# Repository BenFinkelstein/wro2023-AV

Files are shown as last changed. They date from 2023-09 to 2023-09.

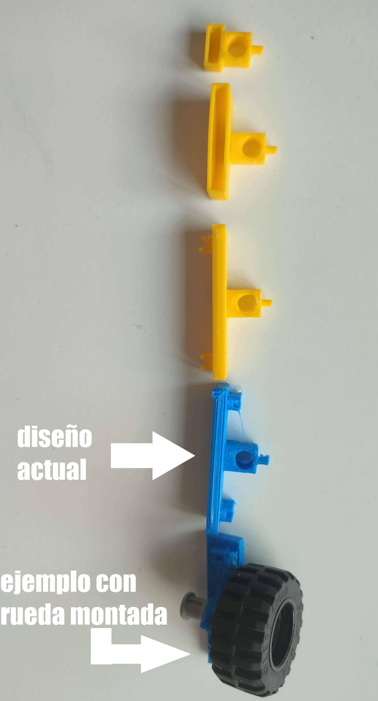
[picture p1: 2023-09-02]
Mobility Management/M.Photos/Montaje de rueda delantera.jpg

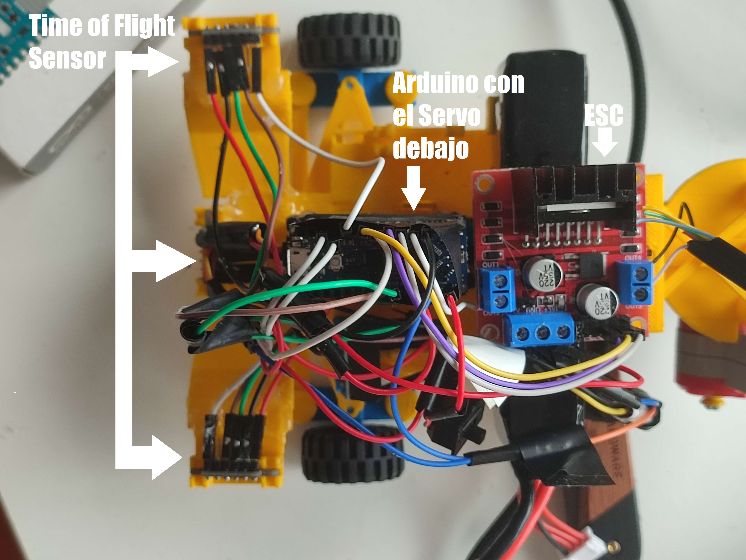
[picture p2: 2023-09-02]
Power and Sense Management/E.Photos/Vista superior de la placa de montaje para los sensores.jpg

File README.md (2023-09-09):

The autonomous vehicle was fully designed from the ground up by the team RoboBros formed by Benjamin Finkelstein Fell and Dimitri Domzalski. 95% of the structures (chassis, steering linkage, sensors board, joints, motor platform, etc.) were printed on a 3D printer. The vehicle is controlled by an Arduino Nano Every. The robot also uses three VL53L0X TOF Sensors, one QMC5883L Magnetometer, one TCS230/TCS3200 Color Sensor, one 13Kg Digital Servo and one Lego Mindstorm DC Large Motor connected to an L298N H-Bridge ESC (Electronic Speed Controller). As a power source, the vehicle uses an 11.1v Li-Po battery to supply power to the Arduino, the servo and the DC motor. The three TOF sensors, the magnetometer and the color sensor get their power supply directly from the Arduino. The code has been developed, compiled and transferred into the Arduino using the Arduino IDE 2.1.1.

Arduino and its IDE were chosen because of their proven reliability and their wide range of features. The readily available libraries, already included in the IDE or easily downloaded from the Internet and installed, was another reason for the selection.

These libraries are needed to interact correctly and successfully with all of the electronic components. Once installed they give access to the functions and variables that allow the code to use the components.

The functions in these libraries are defined in the following header files:

#include "Adafruit_VL53L0X.h"

#include <Servo.h>

#include "Wire.h"

#include <QMC5883L.h>

VL53L0X TOF Sensor uses a combination of an invisible micro laser and a sensor to detect the time the laser takes to hit and bounce off an object in its field of view (Time Of Flight). This particular sensor was chosen because its price/performance in addition to its range, makes sense for a project like this one. The one drawback of sensors at this price range is the erratic behavior, where very often they return bad raw data in the form of inaccurate distance reading. The team partially solved this problem by normalizing groups of readings by eliminating anomalies and averaging the rest of readings.

The team first tested a gyro but it proved to unreliable to guide the vehicle. The team then switch to a magnetometer, which when its raw data is correctly processed helps the vehicle maintain the desire course far better than the gyro.

The TCS230/TCS3200 Color Sensor was selected as the tool to identify the color of the obstacle in order to decide with side to drive by. With the help of an 8 x 8 array of photodiodes it senses color light. After first calibrating the sensor for the specific light conditions of the room, the results are quite reliable.

The 13Kg servo was considered tough enough to work as the single steering actuator, as in the case of every other component it is controlled through the functions of its own library.

The team finally settled, after testing several different options, on the Lego Mindstorm Large DC motor because because it is well known to the members as they use it in last year's WRO competition and also because it proved to be a simple and reliable solution that interacted easily with the ESC and the Arduino. The ESC is needed to act as a bridge between the Arduino and motor as the Arduino cannot directly supply the required power.

The code, firstly, defines the connections to the Arduino pins of every electronic component in the user defined function setID() and the IDE function setup() by using the functions pinMode() and digitalWrite(), functions predefine in the IDE. For example:

pinMode(in1, OUTPUT);

pinMode(in2, OUTPUT);

pinMode(SHT_LOX0, OUTPUT);

pinMode(SHT_LOX1, OUTPUT);

pinMode(SHT_LOX2, OUTPUT);

digitalWrite(SHT_LOX0, LOW);

digitalWrite(SHT_LOX1, LOW);

digitalWrite(SHT_LOX2, LOW);

It then continues to initialize the aforementioned components with the previously mentioned functions from the library of the components in questions such as compass.init() and servo.attach().

The program reads raw data from the three TOF Sensors (Time of Flight distance sensors), one for the left side,one for the right side and one in front, using the library function ragingTest() and the object variable RangeMilliMeter().

The code interects with Magnetometer with library function read (&x, &y, &z). The resulting values are further processes with the following formula:

atan2(g_iY, g_iX) * 180) / PI) + LocalMagneticDeviationpinMode(enA, OUTPUT);

The heading calculated by this function (correcting a negative value by adding 360) is used to steer the vehicle using the Digital Servo’s library function write() which takes at is only parameter the desired direction in degress.

The DC motor is controlled by the following user defined functions:

void DCRun()

{

digitalWrite(in1, HIGH);

digitalWrite(in2, LOW);

analogWrite(enA, cSPEED);

}

The user defined function DCRun() uses the IDE function digitalWrite() which sets the Arduino Nano Every pin number 6 to HIGH and the pin 4 to LOW to specify the driving direction forward and sets the driving speed, with another IDE function, analogWrite(), and the pin 3 set to the desired speed.

void DCStop()

{

digitalWrite(in1, LOW);

digitalWrite(in2, LOW);

}

The user defined function DCStop() uses the same IDE function digitalWrite() with the Arduino Nano Every pin6 set to LOW and the pin 4 set to LOW to stop the motor from rotating.

The core of the code is written in the IDE function loop() which, as the name implies, runs over and over again the written code inside of this essencial function. This allows for continuous interactions in real-time of all of the components and results in the vehicle being able to drive by constantly being informed of its surroundings: the distances in relation to the outer and inner walls, the distance, direction, and when close enough, the color of the obstacles. This data-stream allows the vehicle to advance in a swerve-like fashion, trying constantly to place itself in the best possible place to accomplish the task at hand, and drive as fast as possible around the circuit and/or evade obstacles.

Preforming a 90 degree turn around the inner corners is accomplished by the user defined function Corner(), in which the code looks for either a wall fast approaching the front sensor, meaning the vehicle is close to the end of that side of the outer wall, or a dramatic increase in the distance to the inner wall read by the left or right, meaning the vehicle has passed the inner wall and has to corner in the direction of the change in distance.

As previously mentioned, the pre-compiling checks, the compiling, the linking with the appropriate libraries and finally, the uploading to the vehicle through a USB to micro-USB cable is done by the Arduino IDE.

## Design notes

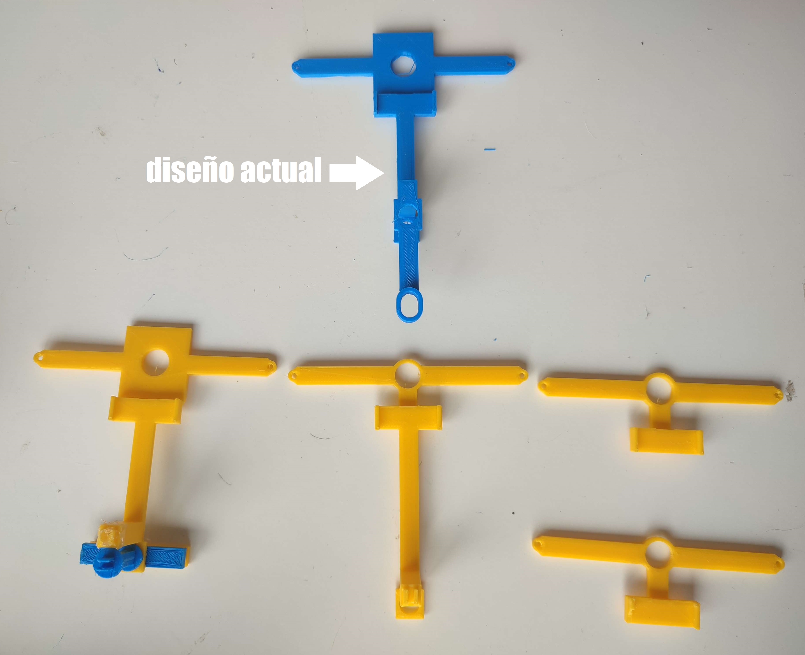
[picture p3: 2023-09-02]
Mobility Management/M.Photos/Chasis.jpg

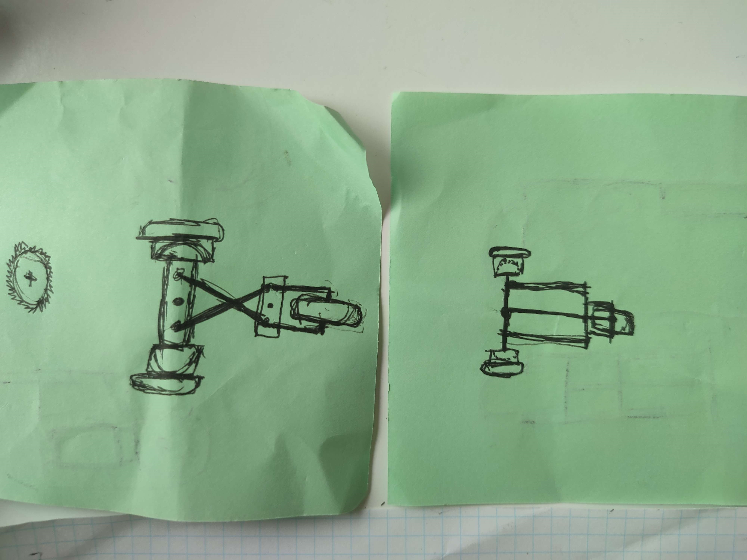
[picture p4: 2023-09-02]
Mobility Management/M.Photos/Dibujos iniciales del sistema de dirección.jpg

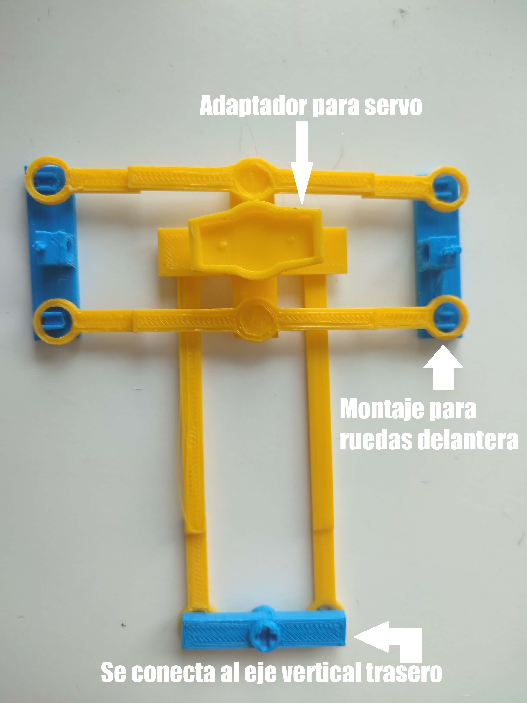
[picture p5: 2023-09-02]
Mobility Management/M.Photos/Dirección delantera.jpg

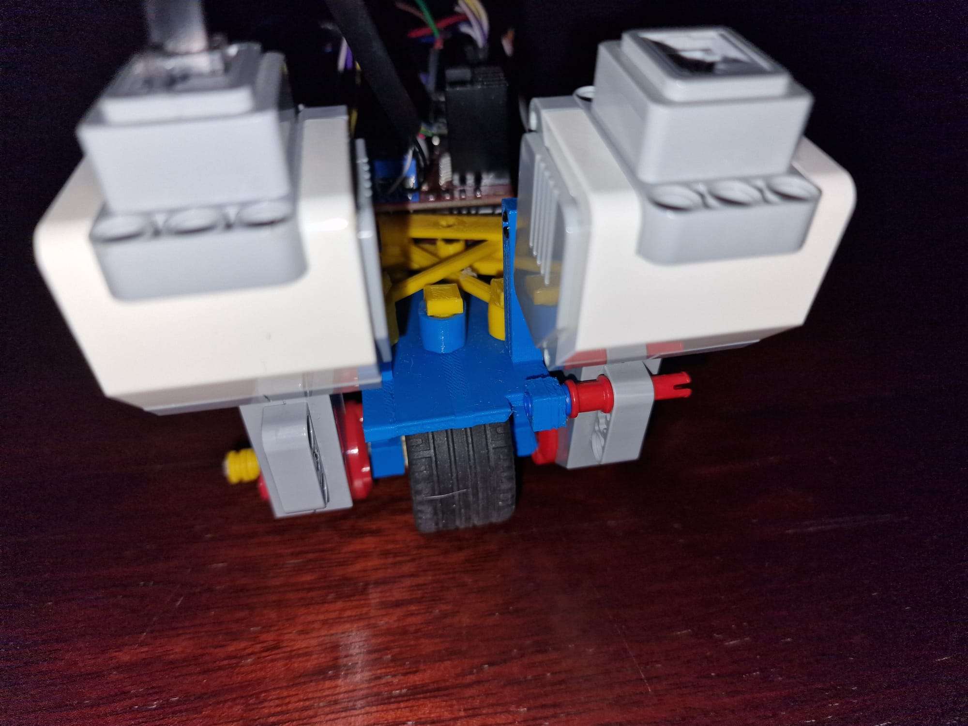
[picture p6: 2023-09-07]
v-photos/vista trasera.jpg

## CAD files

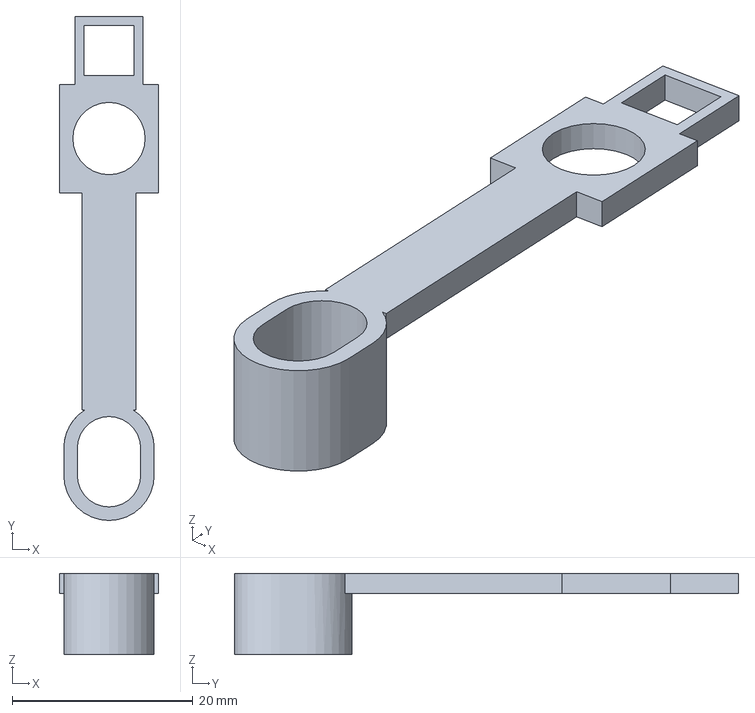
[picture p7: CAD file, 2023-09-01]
models/JOINTmain-Body.3mf
11.0 x 55.8 x 9.00 mm

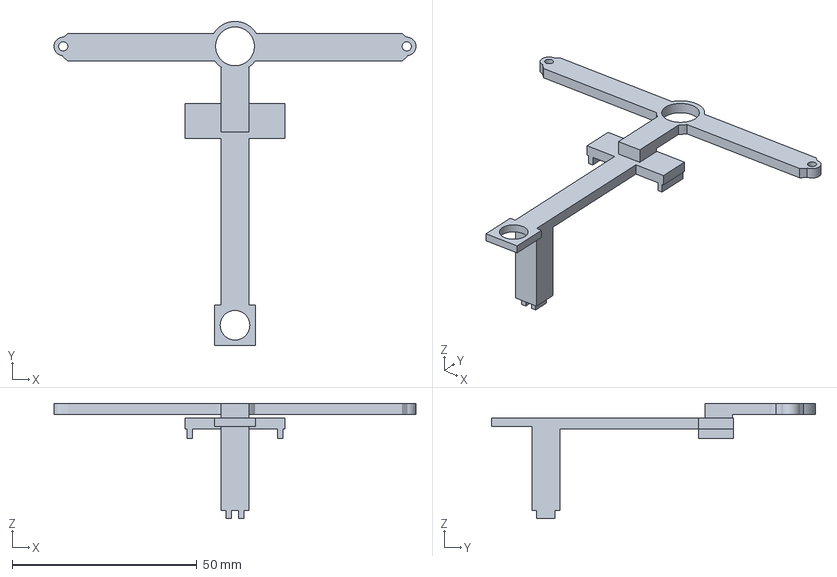
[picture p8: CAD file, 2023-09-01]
models/JOINTmain-Body001.3mf
98.0 x 87.8 x 31.2 mm

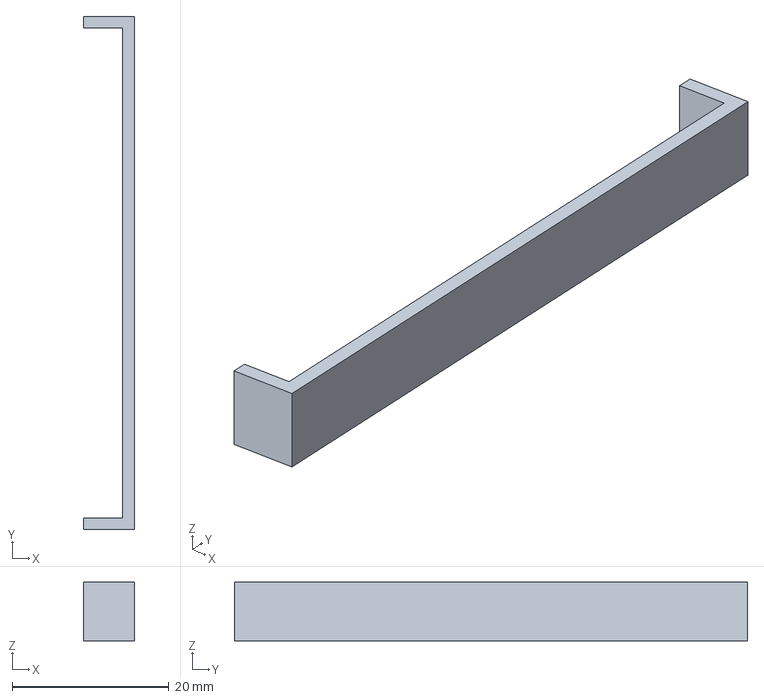
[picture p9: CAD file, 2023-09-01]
models/JOINTmain-Body005.3mf
6.50 x 65.5 x 7.50 mm

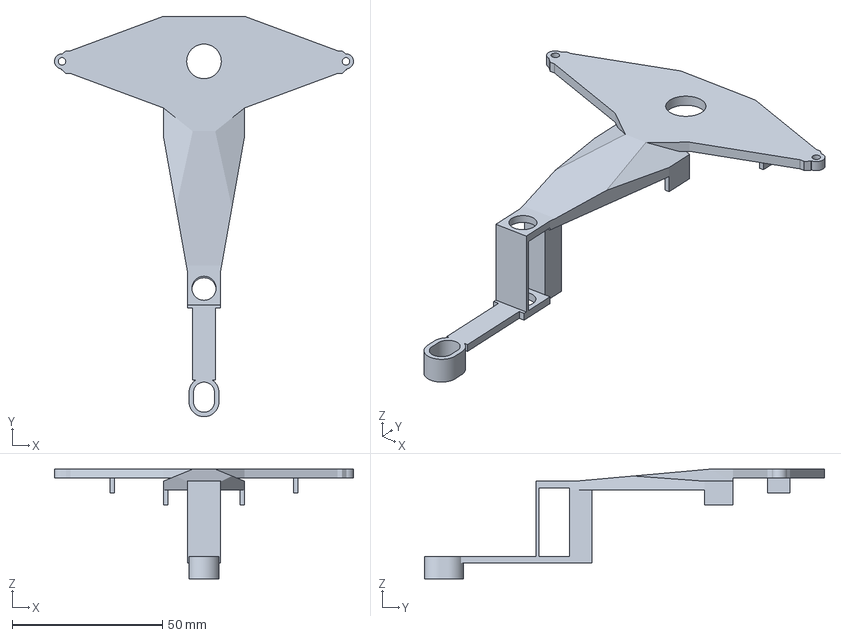
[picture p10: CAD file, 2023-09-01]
models/JOINTmain-Body004.3mf
99.5 x 133.2 x 36.5 mm

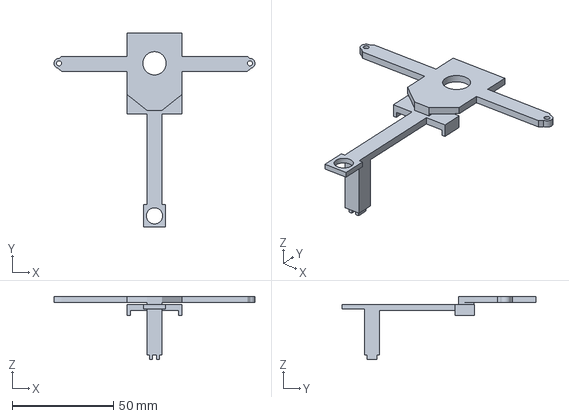
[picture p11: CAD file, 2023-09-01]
models/JOINTmain-Body002.3mf
99.5 x 96.0 x 31.2 mm

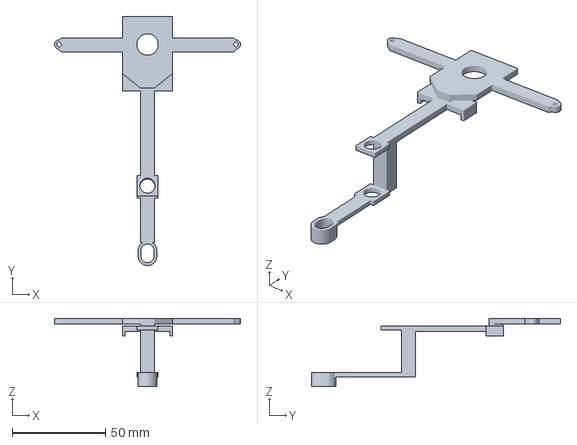
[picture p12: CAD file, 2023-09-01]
models/JOINTmain-Body003.3mf
99.5 x 133.2 x 36.5 mm

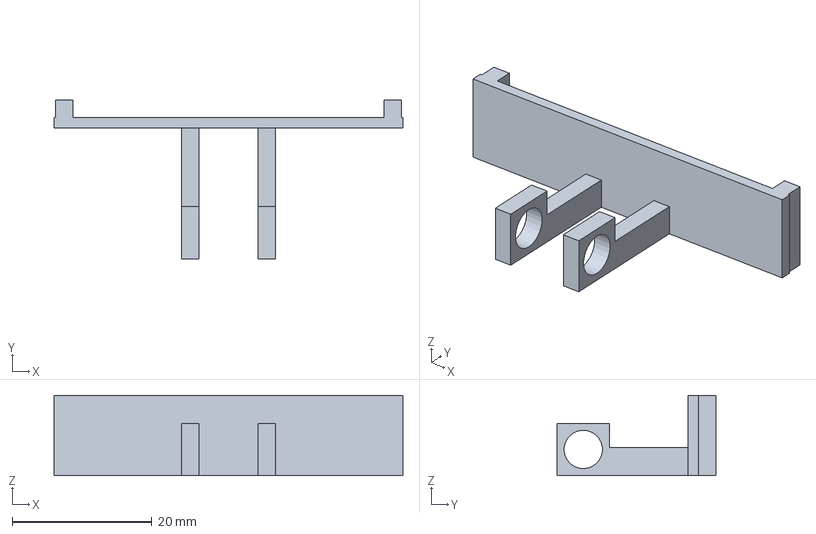
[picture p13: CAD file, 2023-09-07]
models/STEERCOUPLE-Body016.3mf
50.0 x 22.8 x 11.5 mm

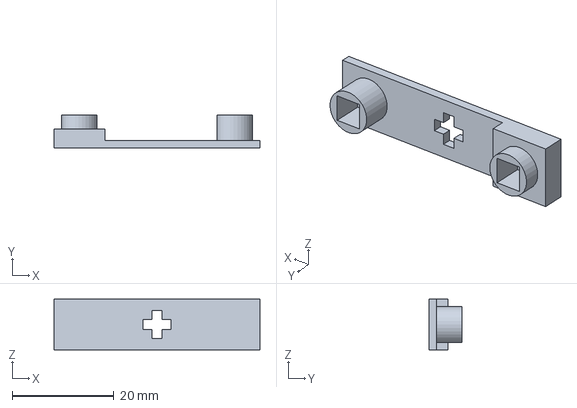
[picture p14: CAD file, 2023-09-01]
models/STEERCOUPLE-Body010.3mf
40.5 x 6.50 x 10.0 mm

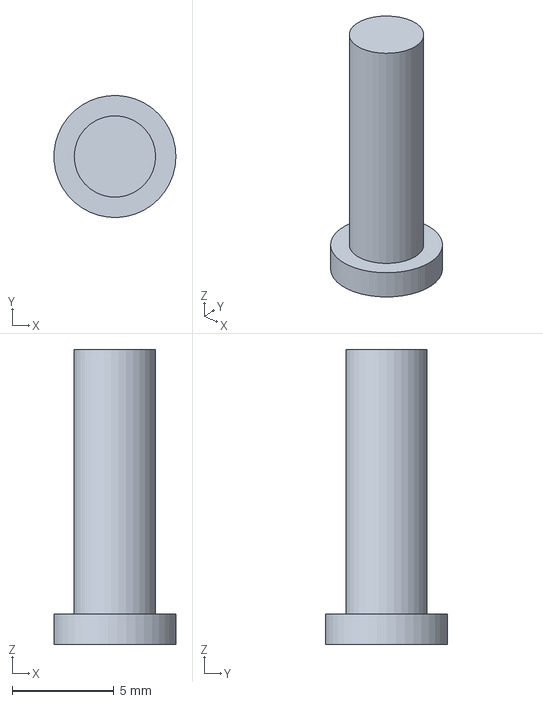
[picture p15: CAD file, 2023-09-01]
models/extra couplers-Body.3mf
5.99 x 6.00 x 14.5 mm

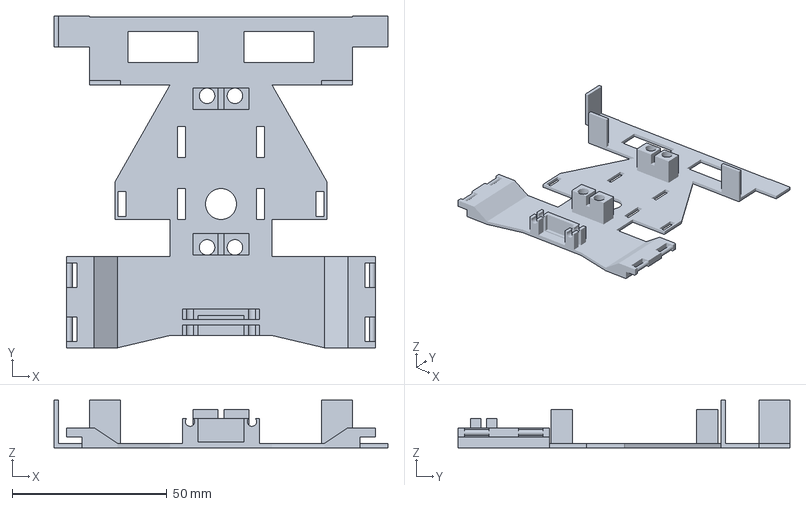
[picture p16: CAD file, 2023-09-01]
models/SensorBoardMAX-Body002.3mf
108.0 x 107.2 x 15.5 mm

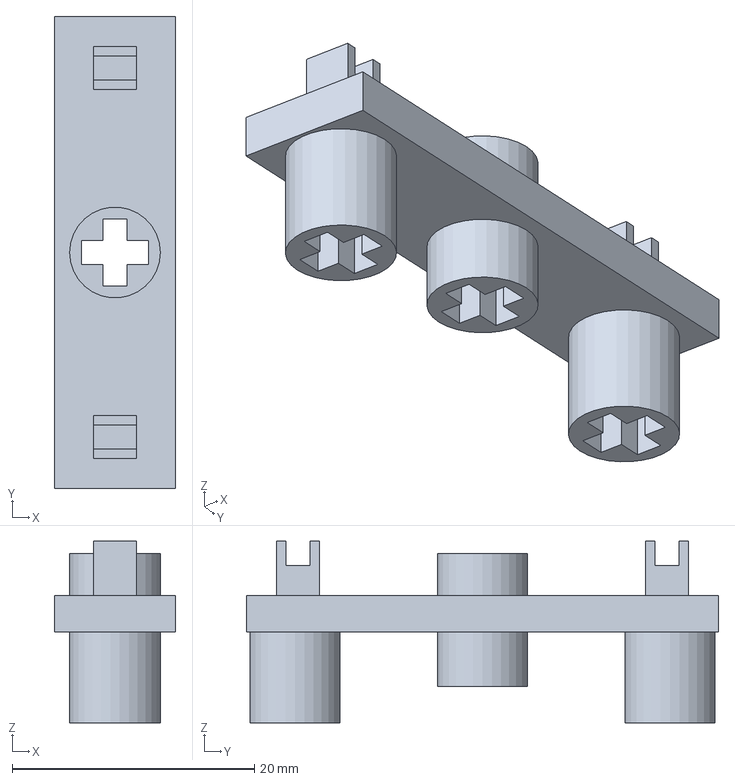
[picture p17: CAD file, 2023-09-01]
models/STEERCOUPLE-Body013.3mf
10.0 x 39.0 x 15.0 mm

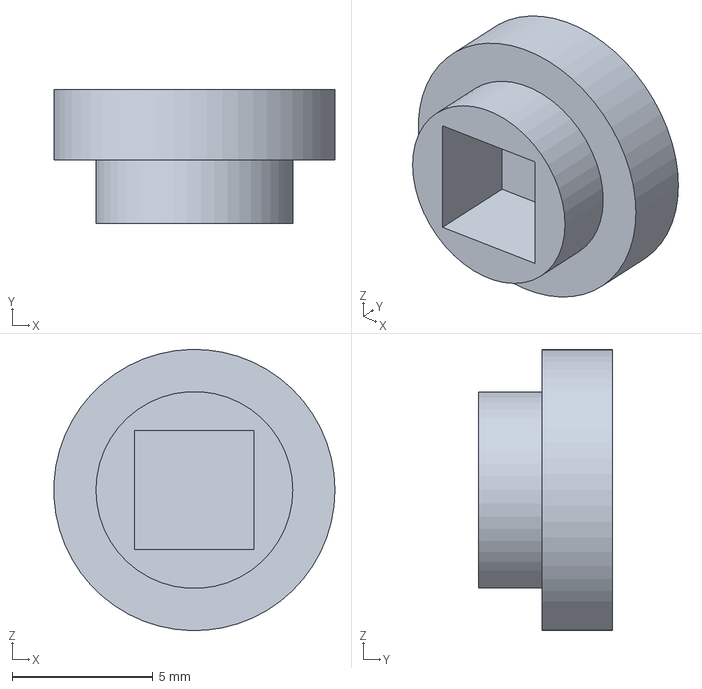
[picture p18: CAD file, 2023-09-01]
models/STEERCOUPLE-Body004.3mf
9.99 x 4.75 x 10.00 mm

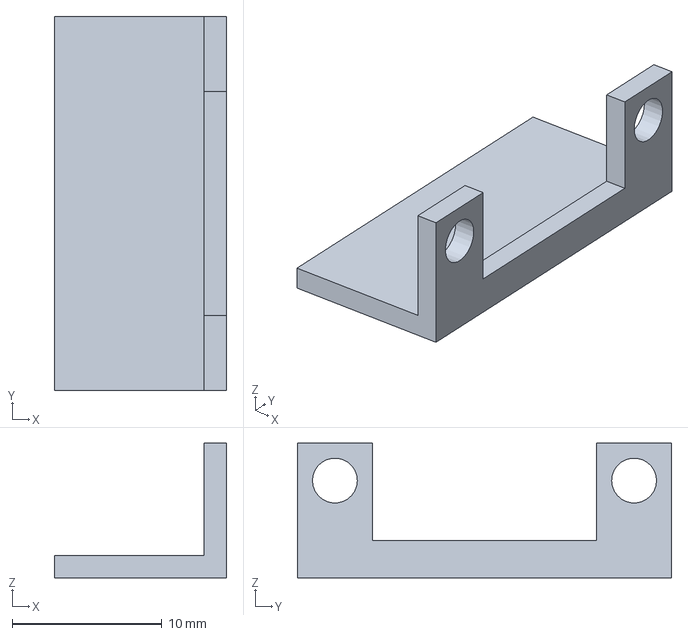
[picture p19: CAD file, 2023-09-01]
models/ToFmount.3mf
11.5 x 25.0 x 9.00 mm

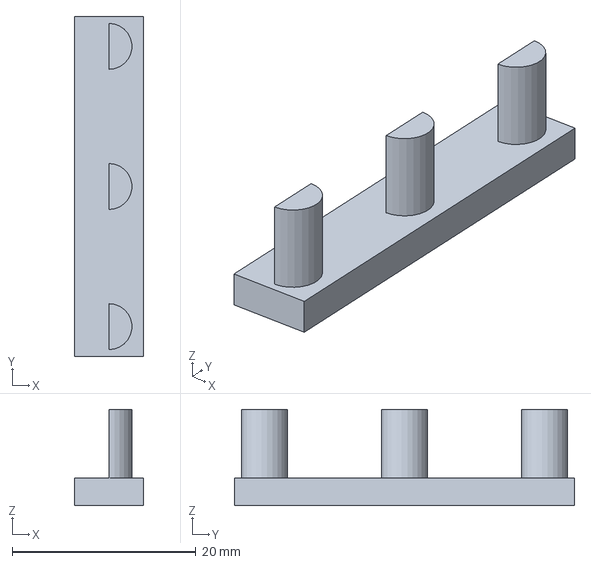
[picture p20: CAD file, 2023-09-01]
models/ROUNDheads-Body.3mf
7.50 x 37.0 x 10.5 mm

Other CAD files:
models/STEERCOUPLE-Body008.3mf
models/FRONTwheelSTEER-Body001.3mf
models/SensorBoardMAX-Body.3mf
models/WheelMount-Body003.3mf
models/EMhead-Body.3mf
models/EngineADAPTER-Body001.3mf
models/EngineADAPTER-Body002.3mf
models/EngineADAPTER-Body003.3mf
models/EngineADAPTER-BodySketch001.3mf
models/EngineMount-Body001.3mf
models/FRONTwheelSTEER-Body.3mf
models/FrontWHEELcoupler-Body.3mf
models/FrontWHEELcoupler-Body002.3mf
models/FrontWHEELcoupler-Body003.3mf
models/HEADS-Body.3mf
models/JOINTtop-Body.3mf
models/Joint-Body.3mf
models/RHmale-Body.3mf
models/STEERCOUPLE-Body.3mf
models/STEERCOUPLE-Body001.3mf
models/STEERCOUPLE-Body002.3mf
models/STEERCOUPLE-Body003.3mf
models/STEERCOUPLE-Body005.3mf
models/STEERCOUPLE-Body006.3mf
models/STEERCOUPLE-Body007.3mf
models/STEERCOUPLE-Body009.3mf
models/STEERCOUPLE-Body011.3mf
models/STEERCOUPLE-Body012.3mf
models/STEERCOUPLE-Body014.3mf
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

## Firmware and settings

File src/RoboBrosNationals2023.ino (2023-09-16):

// Program code for the RoboBros 2023 Automonous Driving Vehicle with a Arduino Nano Every,
// 3 VL53L0X TOF Sensors, 1 LCD, 1 Servo and 1 DC Lego Mindstorm Large Motor
// by Benjamin Fineklstein Fell and Dimitri Domzalski.
// ARDI v2.0 20230915

#include "Adafruit_VL53L0X.h"
#include <LiquidCrystal_I2C.h>
#include <Servo.h>
#include "Wire.h"

#define LOX0_ADDRESS 0x30
#define LOX0_ADDRESS 0x30
#define LOX1_ADDRESS 0x31
#define LOX2_ADDRESS 0x32

#define SHT_LOX0 9
#define SHT_LOX1 10
#define SHT_LOX2 8

#define cSPEED 99
#define cDELAY 50 

#define cFRONT 0
#define cLEFT  1
#define cRIGHT 2

#define cNUMSENSORS  3
#define cNUMSAMPLES  12

#define cSWERVEANGLE 9
#define cCORNERANGLE 17
#define cCENTER      126

#define c1K 1000
#define c8K 8000

#define cCANCEL cNUMSENSORS + 1
#define cTOFTOCALIBRATE cCANCEL

#define cSWERVELEFT  cCENTER - cSWERVEANGLE
#define cSWERVERIGHT cCENTER + cSWERVEANGLE

#define cCORNERLEFT  cCENTER - cCORNERANGLE
#define cCORNERRIGHT cCENTER + cCORNERANGLE

#define cMAXCORNERS 1
#define cMAXSWERVES 2
#define cMINSTOPDST 70

int enA = 3;
int in1 = 6;
int in2 = 4;

bool    g_bCorner, b_bPrintMonitor, g_bDisplayLCD;
uint8_t g_uStatusLox;
int     g_iSensors[cNUMSENSORS], g_iCount8k[cNUMSENSORS], g_iMin[cNUMSENSORS], g_iMax[cNUMSENSORS], g_iFilter, g_iSensor, g_iCanCorner, g_iCornerDir, g_iSwerveDir, g_iLastSwerveDir, g_iCanSwerve, g_iRangeMilliMeter;
double  g_dAverages[cNUMSENSORS];

VL53L0X_RangingMeasurementData_t g_vlSensorVal[cNUMSENSORS];

Adafruit_VL53L0X g_adaLox[cNUMSENSORS];

LiquidCrystal_I2C lcd(0x27,20,4);

Servo g_sSteer;


void setID()
{
  digitalWrite(SHT_LOX0, LOW);
  digitalWrite(SHT_LOX1, LOW);
  digitalWrite(SHT_LOX2, LOW);
  delay(cDELAY);

  digitalWrite(SHT_LOX0, HIGH);
  digitalWrite(SHT_LOX1, HIGH);
  digitalWrite(SHT_LOX2, HIGH);
  delay(cDELAY);

  digitalWrite(SHT_LOX0, HIGH);
  digitalWrite(SHT_LOX1, LOW);
  digitalWrite(SHT_LOX2, LOW);
  delay(cDELAY);

  if (!g_adaLox[cFRONT].begin(LOX0_ADDRESS))
  {
      Serial.println("Failed to boot first VL53L0X @ LOX0_ADDRESS");
      while (true);
  }

  digitalWrite(SHT_LOX1, HIGH);
  delay(cDELAY);

  if (!g_adaLox[cLEFT].begin(LOX1_ADDRESS))
  {
      Serial.println("Failed to boot second VL53L0X @ LOX1_ADDRESS");    
      while (true);
  }

  digitalWrite(SHT_LOX2, HIGH);
  delay(cDELAY);

  if (!g_adaLox[cRIGHT].begin(LOX2_ADDRESS))
  {
      Serial.println("Failed to boot third VL53L0X  @ LOX2_ADDRESS");
      while (true);
  }

  delay(cDELAY);

  for (g_iSensor = 0; g_iSensor < cNUMSENSORS; g_iSensor++)
  {
      g_adaLox[g_iSensor].startRangeContinuous();
      delay(cDELAY);
      g_adaLox[g_iSensor].startRange();
      delay(cDELAY);
  }
}

void DCRunFwd()
{
  digitalWrite(in1, HIGH);
  digitalWrite(in2, LOW);

  analogWrite(enA, cSPEED);

  delay(cDELAY);
}

void DCRunBwd()
{
  digitalWrite(in1, LOW);
  digitalWrite(in2, HIGH);

  analogWrite(enA, cSPEED);
  
  delay(cDELAY);
}

void DCStop()
{
  digitalWrite(in1, LOW);
  digitalWrite(in2, LOW);

  delay(cDELAY);
}

void DCCenter()
{
  g_sSteer.write(cCENTER);

  delay(cDELAY);
}

void lcdPrint(int x, int y, int iSensor)
{
  lcd.setCursor(x,y);

  if (iSensor > cFRONT || g_iSensors[iSensor] < c1K)
      lcd.print(g_iSensors[iSensor]);
  else
      lcd.print("OUT");
}

void lcdSensors()
{
  if (g_bDisplayLCD == true)
  {
    lcd.setCursor(0,0);
    lcd.print("LFT  RHT  FRT DN");
    lcd.setCursor(0,1);
    lcd.print("                ");

    lcdPrint(0,1,cLEFT);

    lcdPrint(5,1,cRIGHT);

    lcdPrint(10,1,cFRONT);

    lcd.setCursor(14,1);
  }
}

void PrintValues(bool bCorner)
{
  Serial.println();
  Serial.print(" >o< ");
  Serial.println(g_iSensors[cFRONT]);
  Serial.print(" <o< ");
  Serial.println(g_iSensors[cLEFT]);
  Serial.print(" >o> ");
  Serial.println(g_iSensors[cRIGHT]);
  Serial.println();

  if (bCorner)
  {
    Serial.print(" )( Cornering ");
  
    if (g_iCornerDir == cLEFT)
        Serial.println("Left...");
    else
        Serial.println("Right...");
  }
  else
  {
      Serial.println();
      Serial.print(" ~o~ Swerve ");

      if (g_iSwerveDir == cLEFT)
          Serial.println("Left...");
      else
          Serial.println("Right...");
  }

  Serial.println();
}

void setup()
{
  g_bDisplayLCD = true,
  
  b_bPrintMonitor = false;
  
  g_iCanCorner = 0;
  
  g_iCanSwerve = 0;

  g_iCornerDir = cFRONT;

  g_iLastSwerveDir = cFRONT;

  lcd.init();

  lcd.backlight();
  lcd.setCursor(0,0);
  lcd.print("Hi! I'm ARDI 2.0");
  lcd.setCursor(0,1);
  lcd.print("by RoboBros 2023");

  Serial.begin(115200);

  while (!Serial) delay(1);
    
  pinMode(enA, OUTPUT);
  pinMode(in1, OUTPUT);
  pinMode(in2, OUTPUT);

  pinMode(SHT_LOX0, OUTPUT);
  pinMode(SHT_LOX1, OUTPUT);
  pinMode(SHT_LOX2, OUTPUT);

  Serial.println("Shutdown pins inited...");

  digitalWrite(in1, LOW);
  digitalWrite(in2, LOW); 
  delay(cDELAY);

  digitalWrite(SHT_LOX0, LOW);
  delay(cDELAY);
  digitalWrite(SHT_LOX1, LOW);
  delay(cDELAY);
  digitalWrite(SHT_LOX2, LOW);
  delay(cDELAY);

  Serial.println("Both in reset mode...(pins are low)");
  Serial.println("Starting...");           
  Serial.println();
  
  setID();

  g_sSteer.attach(5);

  g_sSteer.write(cCENTER);
  delay(500);
  g_sSteer.write(cSWERVELEFT);
  delay(500);
  g_sSteer.write(cCENTER);
  delay(500);
  g_sSteer.write(cSWERVERIGHT);
  delay(500);
  g_sSteer.write(cCENTER);
  delay(cDELAY);

  DCRunFwd();
}

void Swerve()
{
  lcdSensors();

  if (g_iSwerveDir == cLEFT && (g_iLastSwerveDir != g_iSwerveDir || g_iCanSwerve < cMAXSWERVES))
  {  
      g_sSteer.write(cSWERVELEFT);

      delay(200);

      DCCenter();

      g_iCanCorner++;

      if (g_iLastSwerveDir == g_iSwerveDir)
          g_iCanSwerve++;
      else
      {
          g_iCanSwerve = 1;
    
          g_iLastSwerveDir = g_iSwerveDir;
      }

      if (g_bDisplayLCD == true)
        {
          lcd.setCursor(0,0);
          lcd.print("L-SWERVE          ");
          lcd.setCursor(9,0);
          lcd.print(g_iLastSwerveDir);
          lcd.setCursor(12,0);
          lcd.print(g_iSwerveDir);
          lcd.setCursor(15,0);
          lcd.print(g_iCanSwerve);
        }
  }
  else if (g_iSwerveDir == cRIGHT && (g_iLastSwerveDir != g_iSwerveDir || g_iCanSwerve < cMAXSWERVES))
       {  
          g_sSteer.write(cSWERVERIGHT);

          delay(200);

          DCCenter();

          g_iCanCorner++;

          if (g_iLastSwerveDir == g_iSwerveDir)
            g_iCanSwerve++;
          else
          {
            g_iCanSwerve = 1;
        
            g_iLastSwerveDir = g_iSwerveDir;
          }

          if (g_bDisplayLCD == true)
            {
              lcd.setCursor(0,0);
              lcd.print("R-SWERVE          ");
              lcd.setCursor(9,0);
              lcd.print(g_iLastSwerveDir);
              lcd.setCursor(12,0);
              lcd.print(g_iSwerveDir);
              lcd.setCursor(15,0);
              lcd.print(g_iCanSwerve);
            }
        }
        else if (g_bDisplayLCD == true)
              {
                  lcd.setCursor(0,0);  
                  lcd.print("  NOT SWERVE    ");
              }
}

void Corner()
{
  lcdSensors();

  if (g_iCornerDir == cLEFT)
  {
      if (g_bDisplayLCD == true)
      {
          lcd.setCursor(0,0);
          lcd.print("    L-CORNER      ");
      }

      g_sSteer.write(cCORNERLEFT);
  }
  else if (g_iCornerDir == cRIGHT)
      {
          if (g_bDisplayLCD == true)
          {
              lcd.setCursor(0,0);
              lcd.print("    R-CORNER      ");
          }

          g_sSteer.write(cCORNERRIGHT);
      }

  delay(2100);

  DCCenter();

  delay(1500);

  g_iCanCorner = 0; 

  g_iCanSwerve = 0;

  g_iLastSwerveDir = cFRONT;
}

void DCCheckStop()
{
  if (g_iSensors[cFRONT] > 0 && g_iSensors[cFRONT] < cMINSTOPDST)
  {
      DCStop();

      lcd.setCursor(0,0);
      lcd.print("                ");
      lcd.setCursor(0,1);
      lcd.print(" ...STOPPING... ");
    
      lcd.setCursor(5,0);
      lcd.print("[ ");
      lcdPrint(7,0,cFRONT);
      lcd.setCursor(9,0);
      lcd.print(" ]");

      Serial.println(".........STOPING...");
      
      if (g_iLastSwerveDir == cRIGHT)
          g_sSteer.write(cCORNERLEFT);
      else
          g_sSteer.write(cCORNERRIGHT);

      delay(cDELAY);

      DCRunBwd();

      delay(2000);

      DCCenter();
      
      DCStop();

      DCCenter();

      if (g_iLastSwerveDir == cRIGHT)
          g_sSteer.write(cCORNERRIGHT - 3);
      else
          g_sSteer.write(cCORNERLEFT + 3);

      DCRunFwd();

      delay(350);

      DCCenter();
  }
}

void loop()
{
  g_bCorner = false;

  for (g_iSensor = 0; g_iSensor < cNUMSENSORS; g_iSensor++)
  {
      g_iMax[g_iSensor] = 0;
      g_iSensors[g_iSensor] = 0;
      g_iCount8k[g_iSensor] = 0;
      g_dAverages[g_iSensor] = 0.0; 
  
      g_iMin[g_iSensor] = 9999;
  }

  for (g_iFilter = 0; g_iFilter < cNUMSAMPLES; g_iFilter++)
  {
    for (g_iSensor = 0; g_iSensor < cNUMSENSORS; g_iSensor++)
    {
        g_iRangeMilliMeter = 0;

        do
        {
            g_adaLox[g_iSensor].waitRangeComplete();
            g_uStatusLox = g_adaLox[g_iSensor].readRangeStatus();

            g_iRangeMilliMeter++;

            if (g_iSensor == cTOFTOCALIBRATE)
            {
                Serial.print("        Sensor: ");
                Serial.print(g_iSensor);
                Serial.print("  Error status: ");
                Serial.print(g_uStatusLox);
                Serial.print("  Reads: ");
                Serial.println(g_iRangeMilliMeter);
            }
        } while (g_uStatusLox != VL53L0X_ERROR_NONE && g_iRangeMilliMeter < 10);

        g_iRangeMilliMeter = g_adaLox[g_iSensor].readRange();

        if (g_iRangeMilliMeter > c8K)
            g_iCount8k[g_iSensor]++;
        else
        {
          if (g_iRangeMilliMeter < g_iMin[g_iSensor])
              g_iMin[g_iSensor] = g_iRangeMilliMeter;

          if (g_iRangeMilliMeter > g_iMax[g_iSensor])
              g_iMax[g_iSensor] = g_iRangeMilliMeter;

          g_dAverages[g_iSensor] += g_iRangeMilliMeter;
        }

        if (g_iSensor == cTOFTOCALIBRATE)
        {
            Serial.print("[");
            Serial.print(g_iFilter);
            Serial.print(", ");
            Serial.print(g_iSensor);
            Serial.print("] ");
            Serial.print(g_iRangeMilliMeter);
            Serial.print("-> ");
            Serial.print(g_dAverages[g_iSensor]);
            Serial.print("-> ");
            Serial.println(g_iCount8k[g_iSensor]);
        }
     }
  }

  for (g_iSensor = 0; g_iSensor < cNUMSENSORS; g_iSensor++)
  {
      if (g_iCount8k[g_iSensor] > (int)(cNUMSAMPLES * 0.9))
      {
          g_iSensors[g_iSensor] = c8K; 

          if (g_iSensor != cFRONT && g_iCanCorner > cMAXCORNERS && (g_iCornerDir == cFRONT || g_iCornerDir == g_iSensor))
          {
              g_bCorner = true;

              if (g_iCornerDir == cFRONT)
                  g_iCornerDir = g_iSensor;
          }
      }
      else if (g_iCount8k[g_iSensor] == (cNUMSAMPLES - 2))
              g_iSensors[g_iSensor] = (int)(g_dAverages[g_iSensor] / 2.0);
           else
              g_iSensors[g_iSensor] = (int)((g_dAverages[g_iSensor] - g_iMin[g_iSensor] - g_iMax[g_iSensor]) / (cNUMSAMPLES - g_iCount8k[g_iSensor] - 2.0));

      if (g_iSensor == cTOFTOCALIBRATE)
      {
          Serial.println();
          Serial.print("[");
          Serial.print(g_iSensor);
          Serial.print("] ");
          Serial.print(g_dAverages[g_iSensor]);
          Serial.print(" - ");
          Serial.print(g_iMin[g_iSensor]);
          Serial.print(" - ");
          Serial.print(g_iMax[g_iSensor]);
          Serial.print(" / ");
          Serial.println((cNUMSAMPLES - g_iCount8k[g_iSensor] - 2));
      }
  }

  lcdSensors();
  
  /*DCStop();
  delay(1000);
  DCRunFwd();*/

  if (g_iSensors[cRIGHT] > g_iSensors[cLEFT])
      g_iSwerveDir = cRIGHT;
  else
      g_iSwerveDir = cLEFT;

  if (b_bPrintMonitor == true)  
      PrintValues(g_bCorner);

  DCCenter();

  DCCheckStop();

  if (g_iSensors[cRIGHT] != c8K || g_iSensors[cLEFT] != c8K)
      if (g_bCorner == true)
          Corner();
      else
          Swerve();
}
